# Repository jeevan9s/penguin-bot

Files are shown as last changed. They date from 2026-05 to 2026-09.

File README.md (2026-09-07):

# penguin

> <b>P</b>erception-<b>E</b>nabled <b>N</b>avigation and <b>G</b>eneral-<b>U</b>tility <b>IN</b>telligence

Hybrid differential legged-wheeled biped rover for embodied AI, computer vision, and autonomous navigation.

### Status

> - Controller manufactured and partially assembled.
> - Soldering and hardware validation in progress.
> - Mechanical components currently being printed.

<details>`
<summary><strong>Table of Contents</strong></summary>

- [penguin](#penguin)
    - [Status](#status)
  - [Overview](#overview)
  - [Features](#features)
    - [Controller](#controller)
    - [Mechanical](#mechanical)
  - [Architecture](#architecture)
    - [Systems](#systems)
  - [Electrical](#electrical)
    - [Power System](#power-system)
    - [Microcontroller](#microcontroller)
    - [Motor Drivers](#motor-drivers)
    - [Vision Interface](#vision-interface)
    - [Sensor and I2C Interface](#sensor-and-i2c-interface)
    - [Bugs](#bugs)
  - [Mechanical](#mechanical-1)
    - [Chassis](#chassis)
    - [Leg Assembly](#leg-assembly)
  - [Firmware](#firmware)
    - [Architecture](#architecture-1)
    - [Drivers](#drivers)
    - [Engine](#engine)
      - [State \& System Definitions](#state--system-definitions)
      - [Controllers \& Locomotion](#controllers--locomotion)
      - [Behaviour](#behaviour)
    - [Networking](#networking)
    - [GUI](#gui)
  - [Gallery](#gallery)

</details>

I built penguin cause I wanted to create an intelligent robot from the ground up.

<table>
  <tr>
    <td width="50%">
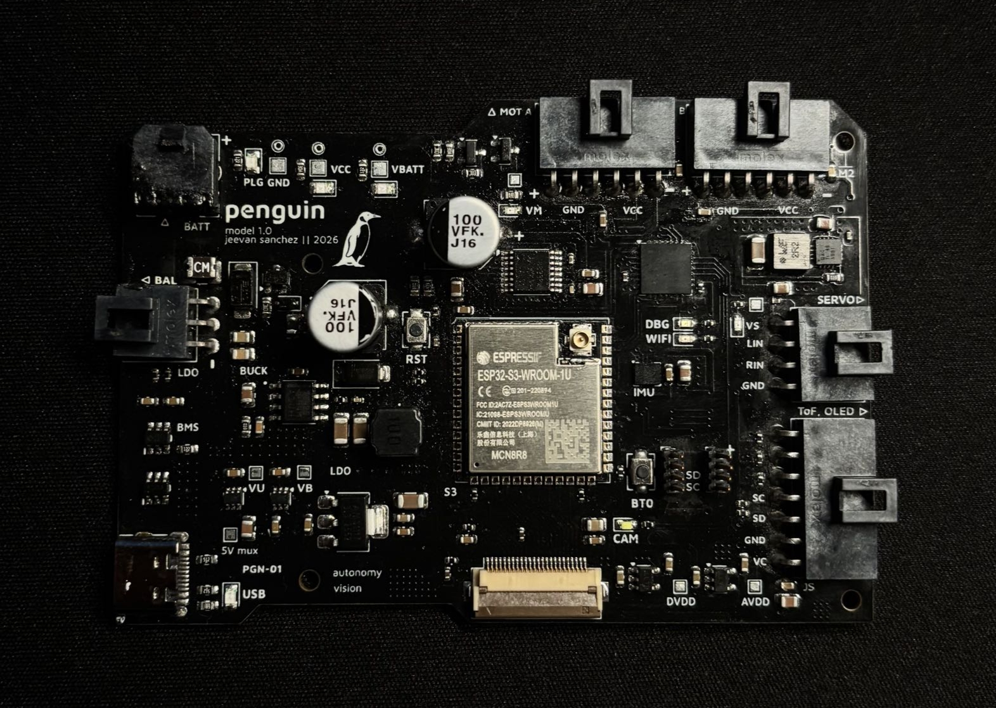
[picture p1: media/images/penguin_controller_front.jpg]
      
    </td>
    <td width="50%">
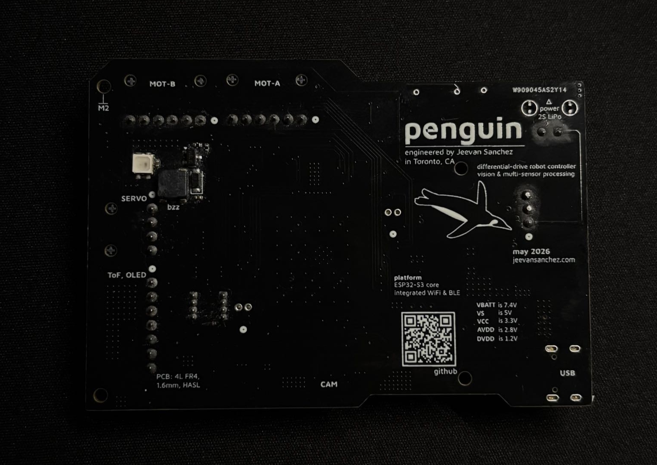
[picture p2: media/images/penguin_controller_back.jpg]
      
    </td>
  </tr>
  <tr>
    <td width="50%">
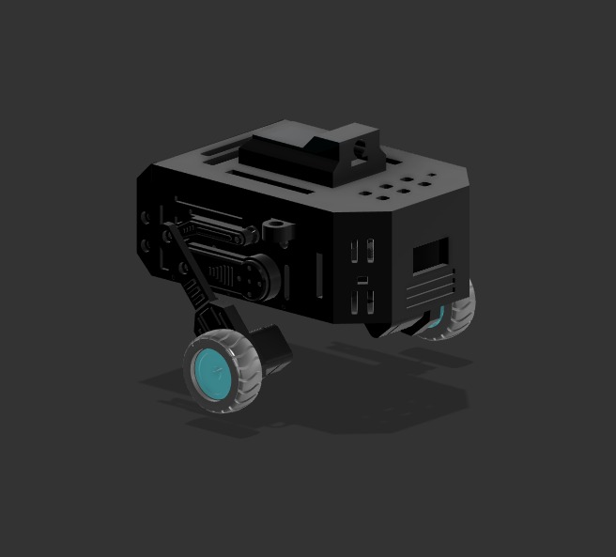
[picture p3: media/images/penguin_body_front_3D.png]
      
    </td>
    <td width="50%">
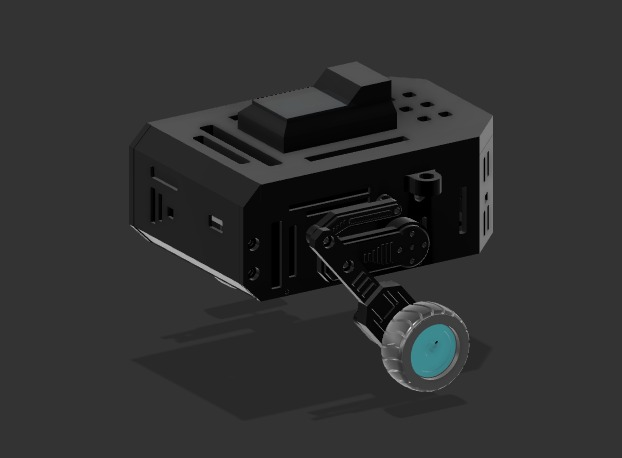
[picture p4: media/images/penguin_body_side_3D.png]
      
    </td>
  </tr>
    <tr>
    <td width="50%">
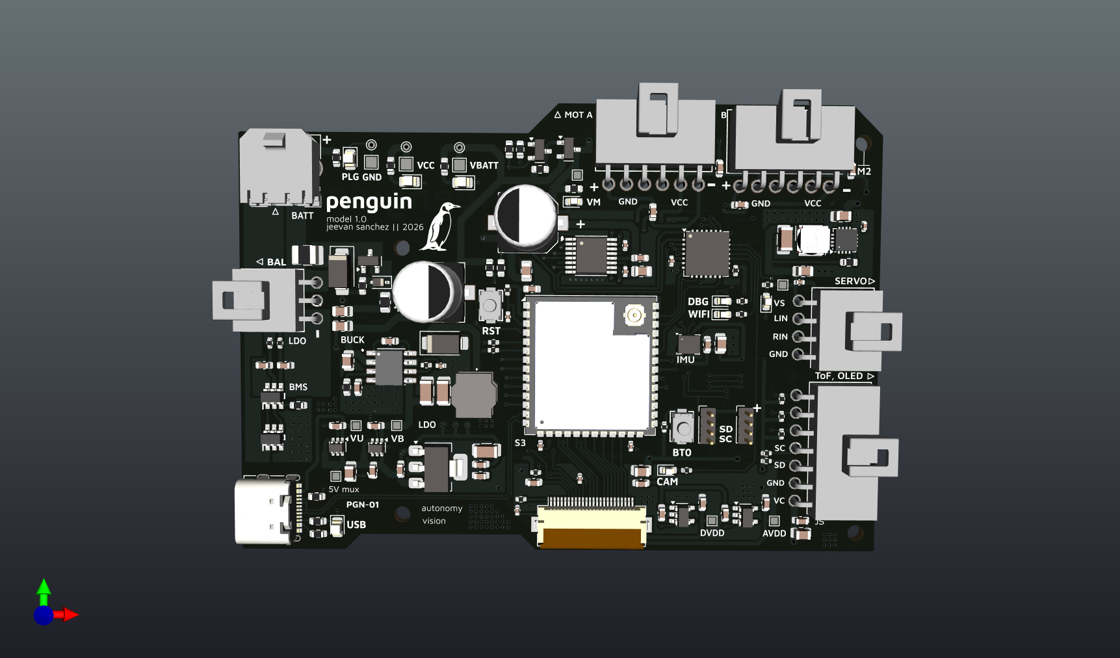
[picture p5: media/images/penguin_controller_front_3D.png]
      
    </td>
    <td width="50%">
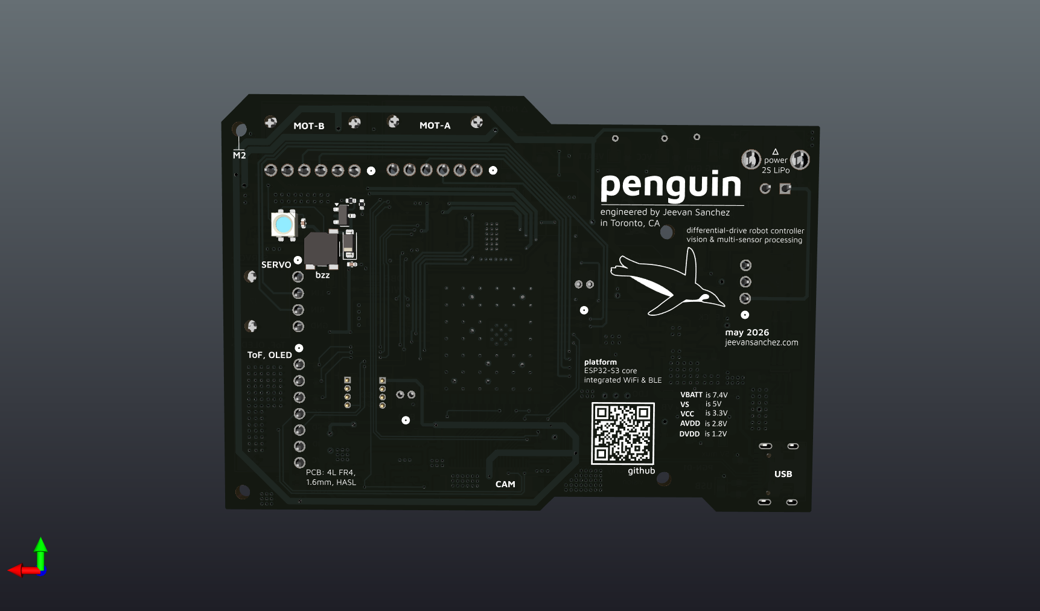
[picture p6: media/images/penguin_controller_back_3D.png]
      
    </td>
  </tr>
</table>

## Overview

Put simply, Penguin is a platform for experimentation with intelligent robotics.

The project began as a simpler, maze-solving rover for a course project (MREN 178 - DSA). My team couldn't deliver the rover in time
so we scaled down. I had already started with hardware, which pushed me to adopt the project into my own, with the intent to expand it past maze-solving.

After that term (Winter '26), I designed a controller PCB and the necessary compoments for the chassis.

Now its September, and I'm tuning PID.

## Features

### Controller

The controller is powered by a 7.4V LiPo Battery and driven by an ESP32-S3 (N16 1U).

Below is a list of features from power circuits to various peripherals.

- Power-entry circuitry with OC/OV protetction, RPP, PI-filter, and dual-mosfet BMS.
- Regulation circuit featuring buck converter, 5V ORing, and LDO for logic power (3V3)
- ESP32-S3 breakout circuitry with USB differential routing, S3 boot mode selection and reset toggle.
- Controlled power delivery via CMOS circuits for main motor power.
- N20 motors with encoders for wheels driven by a DRV8833 chip.
- DS3218 20kg Servo motors for hip joints, driven by PWM signals from S3.
- OV2640 camera with FPC connector and three-level voltage regulation.
- I2C bus with three ToF sensors, OLED screen, and GPIO expander.
- Audible and visual indicators.
- cool silkscreen penguin.

### Mechanical

- Three-layer internal stackup for housing motors, controller board, and routing cables.
- Integrated vents and ports for sensors and devices, air flow, and weight reduction.
- Hybrid locomotion system with wheels and legs.
- Multi-bar leg assembly - pivot arm, mounting arm (hip), leg.

## Architecture

### Systems

## Electrical

This section provides low-level explanations of the significant circuits of each "module" of the controller.

I encourage you to clone the repo or you use [KiCanvas](https://kicanvas.org/) to look at the schematic and board files.

All electronics were designed with **KiCad**.

### Power System

**Power Entry**

<p align="center">
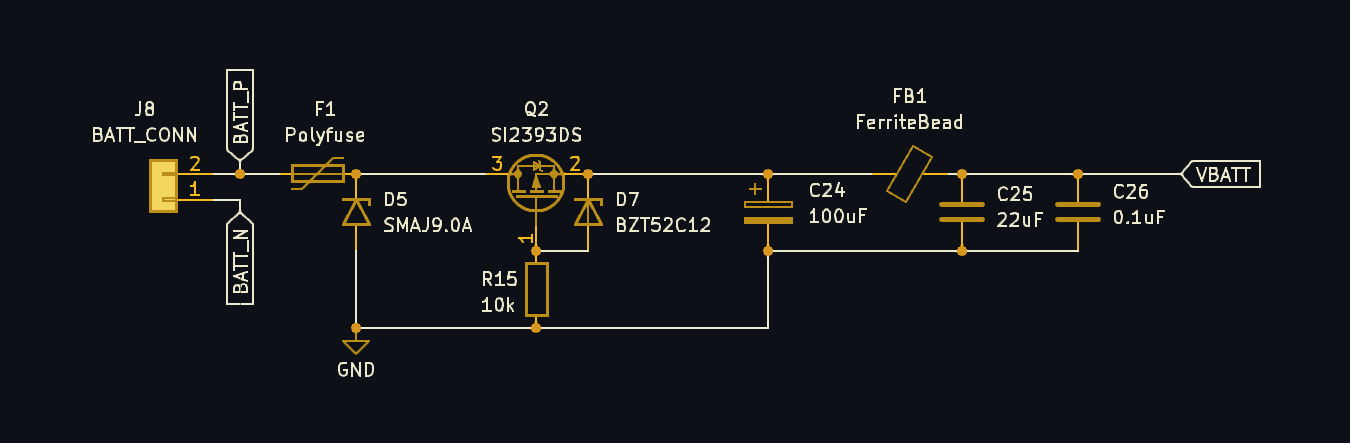
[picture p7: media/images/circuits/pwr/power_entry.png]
  
</p>

The 7.4V battery power enters through a Molex Micro-Fit (3mm Pitch) header, where it is then met with a 12V 7A fuse for over-current protection. A PTC resettable fuse was selected for durability.

The positive battery line is then protected from voltage spikes with a Transient Voltage Supression (TVS) diode placed in paralell for clamping.

- The diode's standoff @ `9V`
- Breakdown @ `10V`
- Clamps @ `15.4V`

The positive line then goes through a Reverse Polarity Protection (RPP) circuit, using a P-Channel MOSFET for lossless efficiency (lower V drop than standard diodes).

A Zener diode and resistor is placed between the MOSFET's gate and source for gate over-voltage protection.

A bulk electrolytic (100μF) capacitor, ferrite bead, and high-frequency (0.1μF) capacitor are then placed to create a third-order low pass filter (π-filter).

- This is used to smooth voltage spikes and reduce EMI.

The ferrite bead was primariy selected for its saturation current and DCR.

The approximate current draw with safety margin $I_{net}$ is 5A.

$I_{\mathrm{sat}} = 1.5 \times I_{\mathrm{net}} \approx 10 A$

Minimize heat dissipation.

$DCR$ is 10Ω

$P_{heat} = DCR \times I_{\mathrm{sat}} \approx 0.25 W$

**Battery-Management-System (BMS)**

<p align="center">
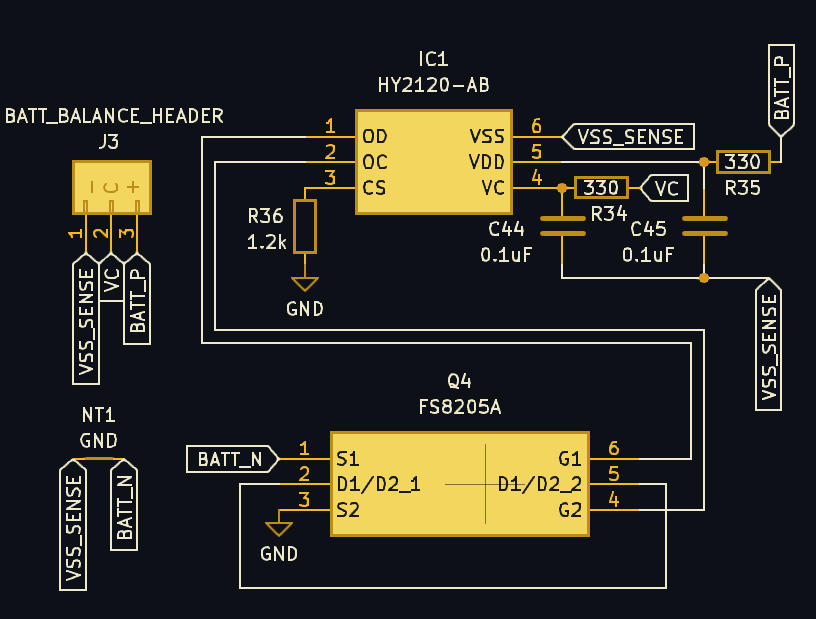
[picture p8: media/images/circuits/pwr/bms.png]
  
</p>

The BMS system uses the negative terminal of the battery and features a `HY2120` protection IC with a dual-mosfet to form the system's **GND**.

The IC uses the balance tap of the battery (VC ~ 3.7V nominal) to monitor the level of Cell 1, while using the main positive terminal (VDD ~ 7.4V nominal) to monitor Cell 2.

This allows the IC to indepdently track each cell's voltage and trigger the dual-MOSFET to cut off power if either cell suffers from overcharge or overdischarge.

**Voltage Regulation (I)**

<p align="center">
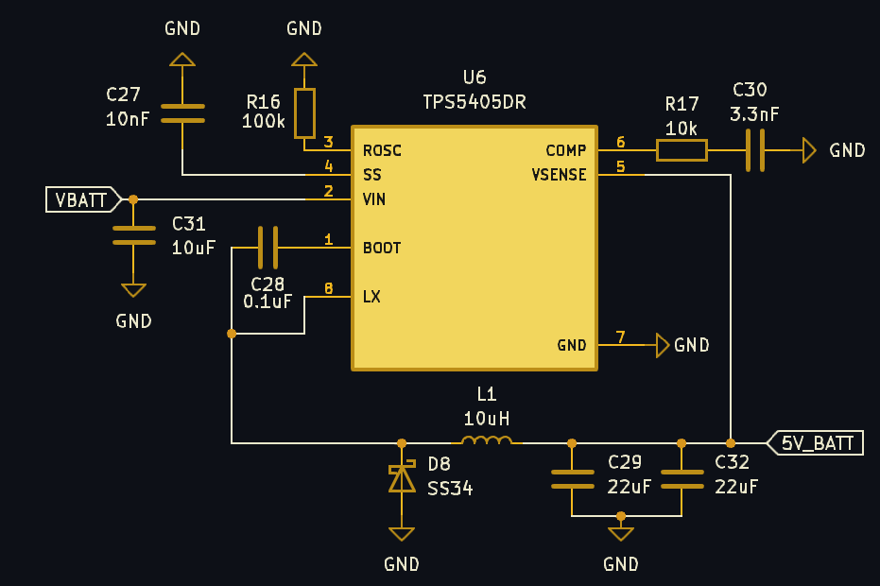
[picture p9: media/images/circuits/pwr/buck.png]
  
</p>

The controller uses a cascade regulation system, starting with the `TPS5405DR` buck converter.

The input voltage is `VBATT` (7.4V), after the protection and filtering circuitry, and the output is 5V.

The $R_{osc}$ value will determine the switching frequency of the converter.

Switching frequency is governed by the relationship.
$$R_{\text{OSC}} (\text{k}\Omega) = 21.82 \cdot f_{\text{SW}}^{-1.167}$$

I chose a value of `100kΩ` for a $f_{SW}$ of approximately `271 kHz`

For the soft-start capacitor $C_{ss}$ , I chose a value of `10nF` for a soft-start time of `5ms`

The values below were taken from the [TPS5405DR Datasheet](https://www.ti.com/lit/gpn/tps5405)

$$
C_{SS} = \frac{t_{SS} \cdot I_{SS}}{V_{REF}}
$$

$$
C_{SS} = \frac{(5\,\mathrm{ms})(2\,\mathrm{\mu A})}{0.8\,\mathrm{V}}
= 12.5\,\mathrm{nF}
\approx 10\,\mathrm{nF}
$$

The inductor values were chosen using the equation below.

$$
L=\frac{V_{out}\left(V_{in}-V_{out}\right)}
{V_{in}f_{sw}\Delta I_L}
$$

Using our calculated $f_{sw}$ from above and our voltage requirements (8.4V in, 5V out):

$$
L=
\frac{(5\,\mathrm{V})(8.4\,\mathrm{V}-5\,\mathrm{V})}
{(8.4\,\mathrm{V})(525\,\mathrm{kHz})(0.3\,\mathrm{A})}

\approx
10\,\mathrm{\mu H}
$$

The Schottky diode is rated for the `2A` output current and `8.4V`

**5V ORing**

<p align="center">
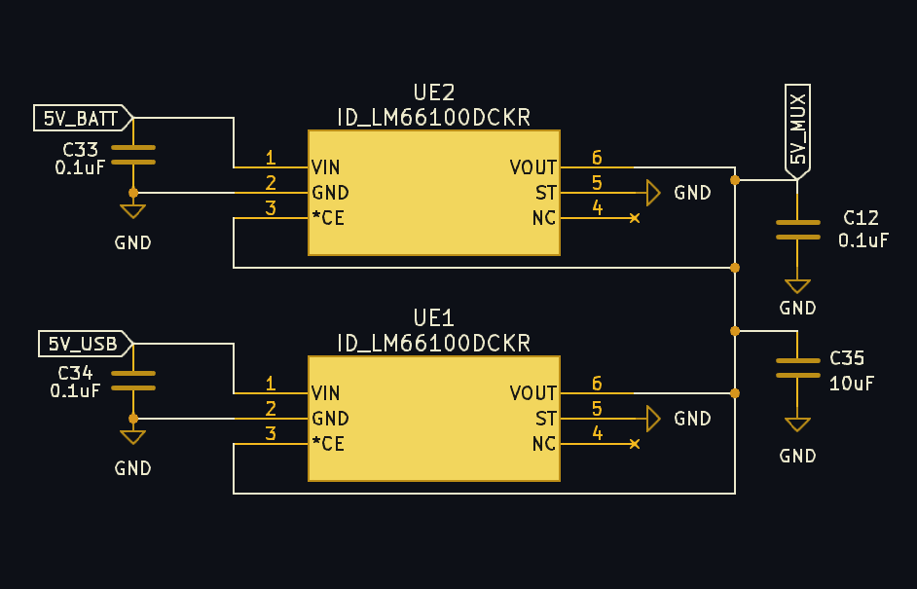
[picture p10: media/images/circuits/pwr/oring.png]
  
</p>

The `5V` rails from both USB and the buck converter are combined using an OR-ing circuit (Dual Ideal Diodes) to prevent backfeeding before feeding the second stage of regulation.

In this configuration, the outputs of both `LM66100` ideal diode controllers are tied together to form the shared `5V` rail. The `CE` pins of each device are also tied to the output rail, ensuring both controllers are only enabled once the rail is present

**Voltage Regulation (II)**

<p align="center">
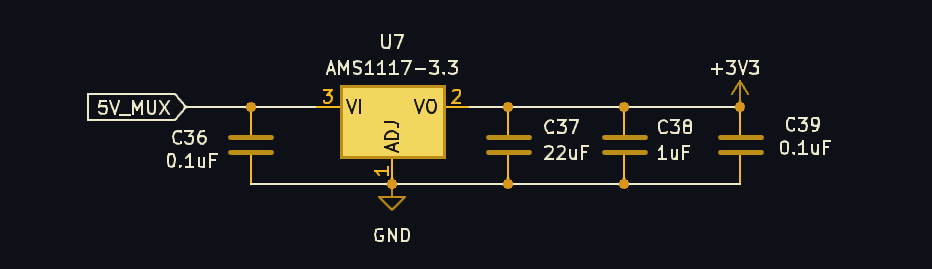
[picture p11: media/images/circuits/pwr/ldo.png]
  
</p>

The second stage of voltage regulation involes a Low-Dropout Regulator (LDO), the `AMS1117`

It is fed the combined `5V` rail from the OR-ing circuit to produce the controller's logic-level voltage: `3V3`

**Controlled Motor Power Delivery**

<p align="center">
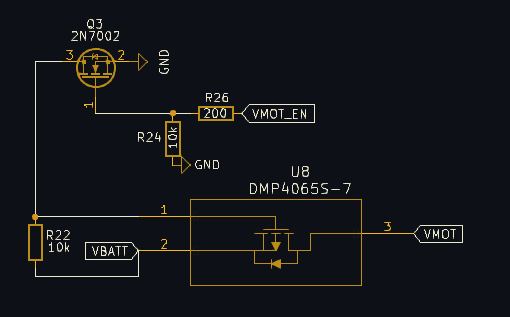
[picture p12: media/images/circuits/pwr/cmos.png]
  
</p>

The power for the N20 and Servo motors is controlled using a complementary-MOSFET (CMOS) setup, driven by a digital `HIGH` from the S3.

- When the control signal is low or floating, the N-channel MOSFET remains off and a pull-up resistor holds the gate of the P-channel MOSFET at the supply voltage, keeping it disabled and disconnecting the load rail.

- When the control signal is driven high, the N-channel MOSFET turns on and pulls the P-channel gate low, creating sufficient gate-source voltage to enable conduction and connect the supply to the load.

This controlled power line, `VMOT = 7.4V` powers the supply voltage of the `DRV8833` chip, and is converted via local buck converter to produce `VSERVO = 5V`

**Voltage Sensing**

A resistor divider circuit is used to produce a signal to be read by the S3's internal ADC.

- $R_1 = 100\,\mathrm{k\Omega}$
- $V_{batt} = 7.4\,\mathrm{V}$
- $V_{out} = 2.8\,\mathrm{V}$

$$
R_2 = \frac{R_1 \cdot V_{out}}{V_{batt} - V_{out}}
$$

$$
R_2 = \frac{100\,000 \cdot 2.8}{7.4 - 2.8}
= 50\,\mathrm{k\Omega}
\approx 47\,\mathrm{k\Omega}
$$

### Microcontroller

The controller is driven by an ESP32-S3-WROOM-1U-N16 microcontroller.

The `U` and `N16` model was selected for layout flexibility and memory capacity (16MB).

A `MCP23017` GPIO expander was used to accomodate space for all digital inputs/outputs (via `I2C`)

**Digital IO**

<p align="center">
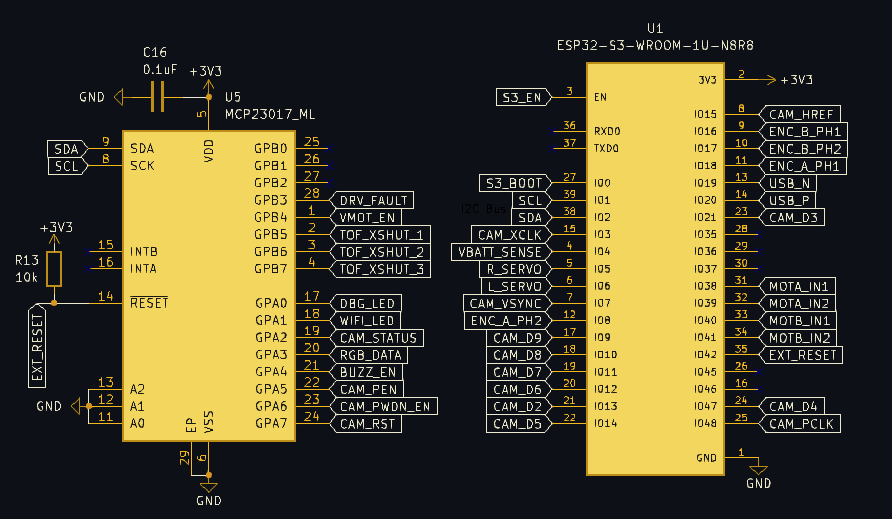
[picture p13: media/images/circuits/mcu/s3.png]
  
</p>

**Mode Select and Reset Toggle**

<p align="center">
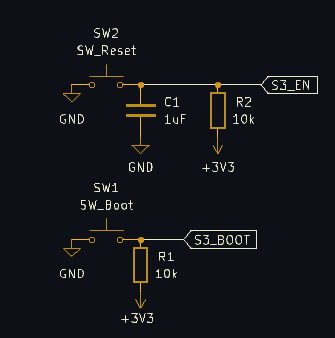
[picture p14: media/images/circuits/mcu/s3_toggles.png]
  
</p>

The S3 can be put into **BOOT** mode and **RESET** with onboard buttons.

**BOOT** mode determines whether the chip runs existing code from flash memory or waits to download new firmware.

- The ESP32 samples the **BOOT** pin (`GPIO0`) during reset to determine the boot mode.
- It is **active-low**: when pulled to **GND** during reset, the chip enters UART bootloader mode for flashing firmware.
- The circuit uses a momentary push-button to **GND** and a `10kΩ` pull-up resistor to ensure a defined high state during normal operation.

| BOOT0 Level | Boot Mode |
| --- | --- |
| HIGH | Programming Mode |
| LOW | Memory Mode |

**RESET** controls the Enable (EN) pin which is the ON/OFF (reset) switch for the ESP32.

- It is **active-low**: when pulled to **GND** it turns off the chip, and when released, it restarts.
- The circuit consists of a momentary push-button, a pull-up resistor to ensure the chip is enabled by default, and a `1µF` capacitor to filter out button noise.

### Motor Drivers

The `N20` wheel hub motors are driven by a `DRV8833` chip, and their encoder signals are routed to digital pins on the `S3`.

They are connected via 6-Pin Molex Nano-Fit (2.50mm Pitch) headers, and feature decoupling across the motor terminals and on the encoder power supply.

<p align="center">
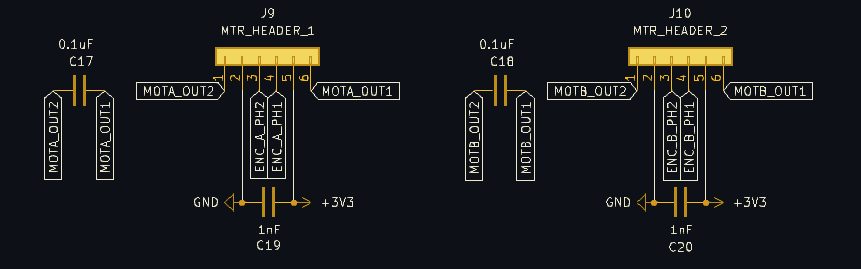
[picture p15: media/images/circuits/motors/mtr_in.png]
  
</p>

The **Servo** hip motors are driven by PWM signals from the `S3`, and are connected by a single 4-Pin Molex Nano-Fit header.

The connector has decoupling on the power supply, and series resistors on the signal lines to improve signal integrity and reduce noise.

<p align="center">
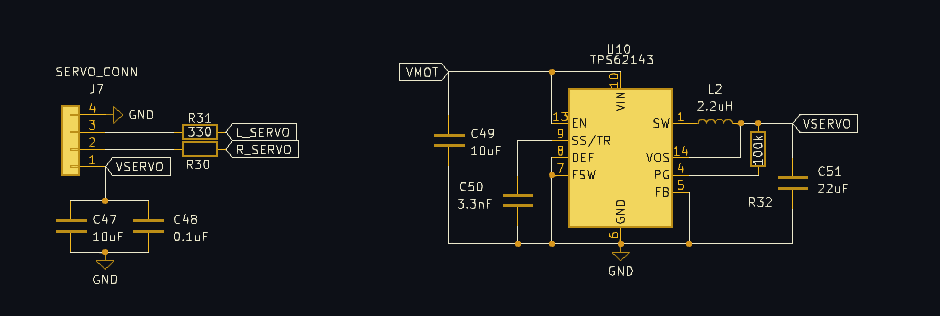
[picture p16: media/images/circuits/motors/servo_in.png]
  
</p>

### Vision Interface

The controller interfaces with an `OV2640` camera via FPC-connector.

The camera is configured in **8-bit** mode using adjacent digital pins for frames.

<p align="center">
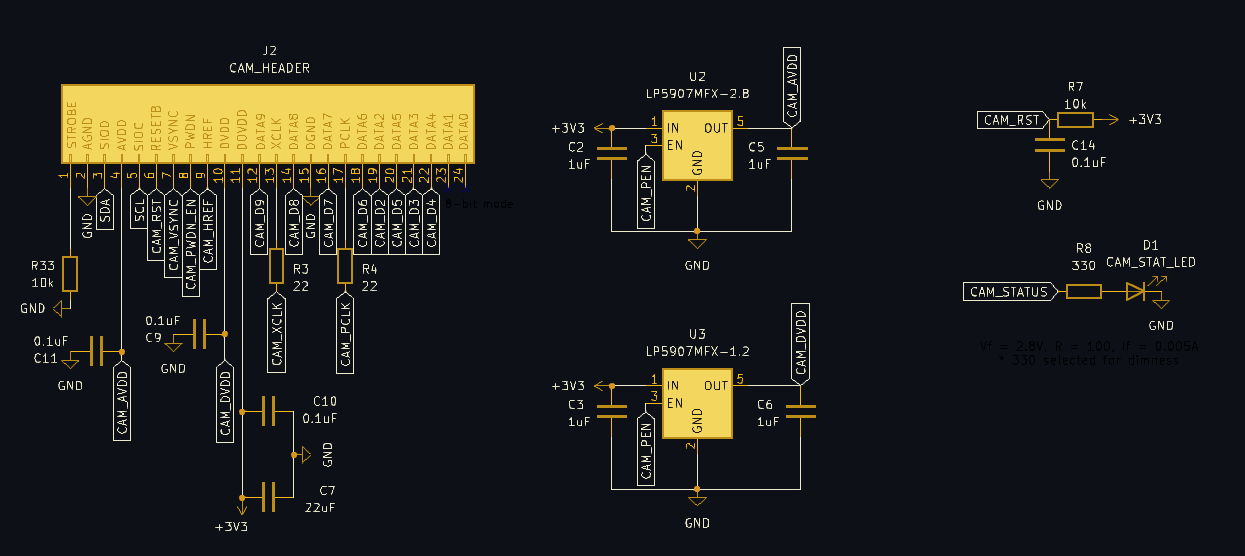
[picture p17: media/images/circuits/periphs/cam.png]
  
</p>

Power supply is divided into three levels:

- `DVDD`: **1.2V**
- `AVDD`: **2.8V**
- `DOVDD`: **3.3V**

These conversions are acheived through the use of fixed-output-voltage LDOs (`LP5907MFX`) with local decoupling.

Series low-resistance resistors were added on the camera's clock signals (PCLK, XCLK) in series for signal integrity and EMI reduction.

- I used only `S3` pins, not expander pins, for the data pins `D2-D9` and `HREF`, `VSYNC` pins.

### Sensor and I2C Interface

The controller interfaces with three `VL53L0X` Time-of-Flight (ToF) sensors for ranging (obstacle detection, SLAM - potentially).

This interface is achieved through `I2C`.

The sensors are connected through a single 7-Pin Molex Nano-Fit header, connecting the sensor power, I2C clock and data signals, and the shutdown `XSHUT` pins of each sensor.

Decoupling capacitors and shutdown pull-ups are placed locally.

<p align="center">
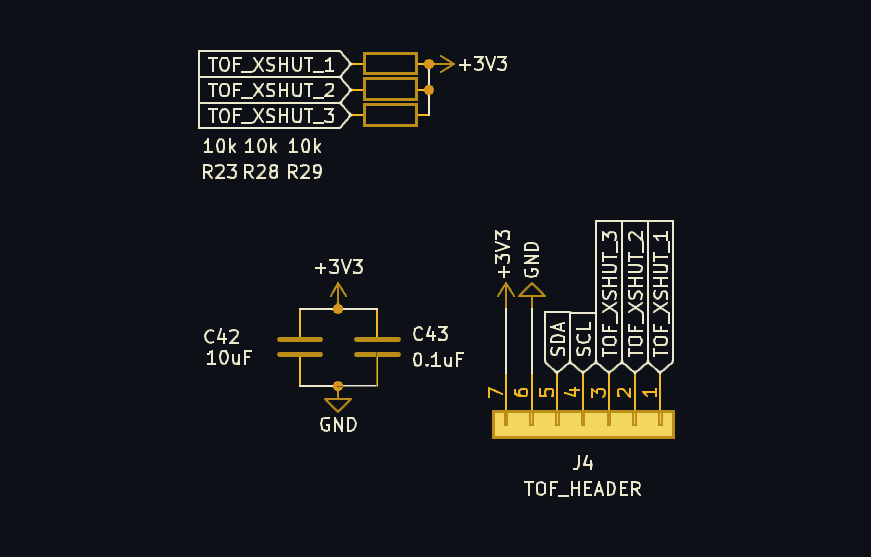
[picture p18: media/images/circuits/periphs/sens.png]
  
</p>

**Additional I2C Devices**

- IMU (LSM6DSL)
- Mini OLED Screen
- OV2640 Cam

**Indicator Components**

- RGB LED
- Passive LEDs for simple indication
- Buzzer for audible indication

### Bugs

- Misoriented cam header -- fixed with an extenison board + B-Type FPC cable
- DRV8833 VM and VINT pins missing GND connection
- Buzzer and RGB LED pins need clock signal but wired to MCP pins.

## Mechanical

This section provides insight on the mechanical components of Penguin: the chassis and leg assembly.

In no way am I a CAD-expert, so this was definitely a learning experience with lots of iteration.

Projected geomtery was clutch.

I used Fusion360 to design everything.

### Chassis

The chassis consists of several components attatched with pegs and magnets.

<p align="center">
  
</p>

**Base Plate**

The base plate forms the start of the internal stack-up.

It contains Servo pads for the hip motors to rest on, a port for an ON/OFF switch, and a battery slot with vents.

It acts as the "floor" of the Servo bay and the bottom of the chassis.

It connects to the rest of the chassis through pegs to insert into the inside face of each wall, as well as the nose.

<p align="center">
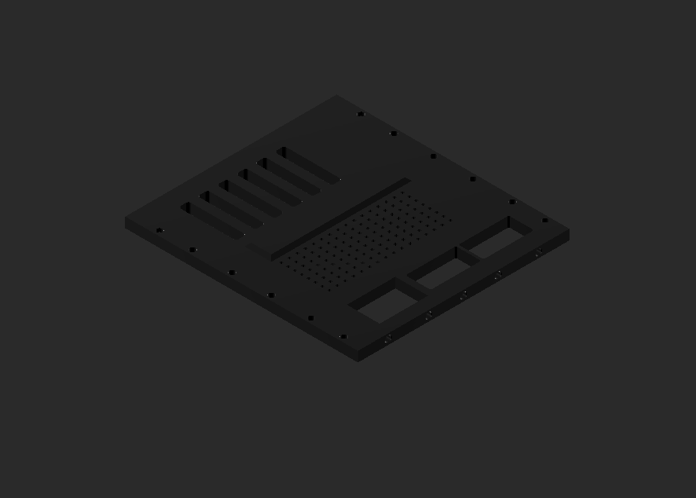
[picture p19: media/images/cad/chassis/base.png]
  
</p>

**Side Walls**

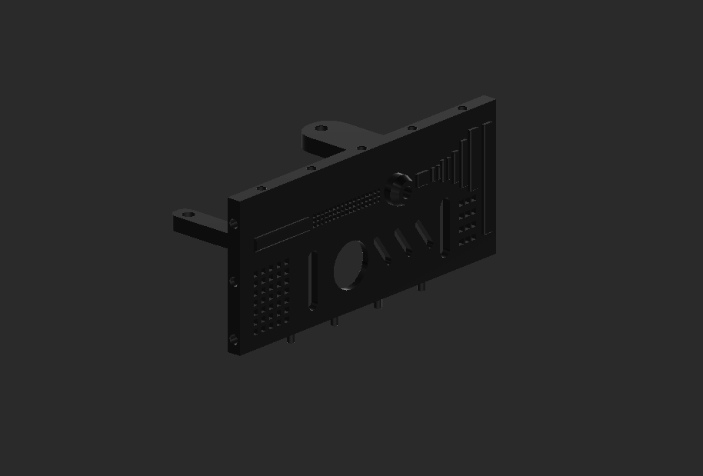
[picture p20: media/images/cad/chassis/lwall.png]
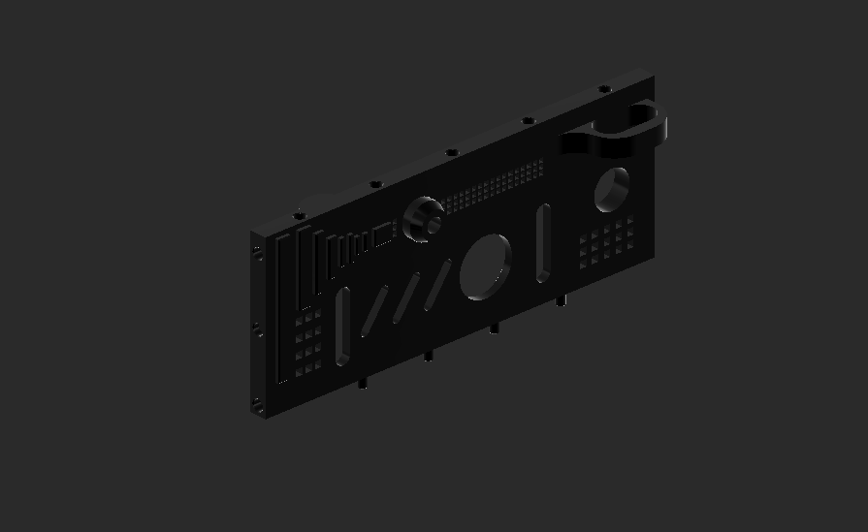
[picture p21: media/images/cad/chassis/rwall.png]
<table><tr><td width="50%"></td><td width="50%"></td></tr></table>

The side-walls enclose the internal stack-up, and provide mounting points for several chassis components.

Mounting tabs are on the inside of each wall for board mounting.

They have cutouts for the Servo shafts, arm joints, and house components like the external antenna.
The top face has short holes for magnets that align with holes on the lid.

**Nose**

<p align="center">
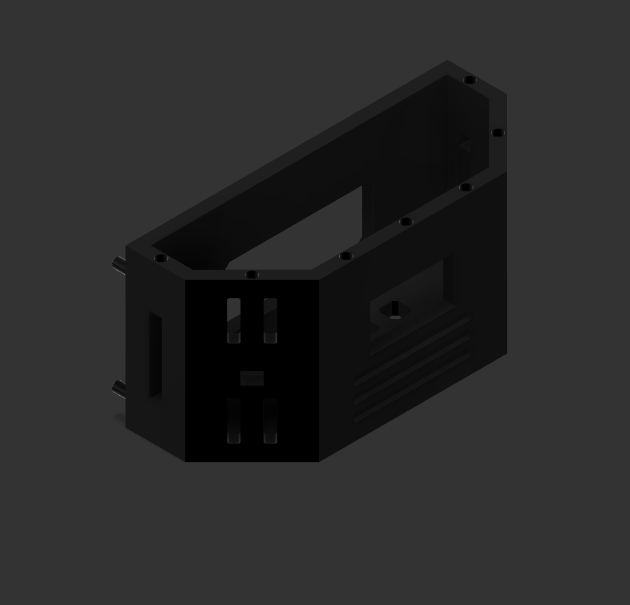
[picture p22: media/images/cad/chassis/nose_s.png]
  
</p>

The nose contains ports for the ToF sensors, and an OLED screen.

There is also an open face cable port connecting to the controller bay for routing.

It mounts to each walls with pegs and magnets, as well as to the base plate.

**Stern**

<p align="center">
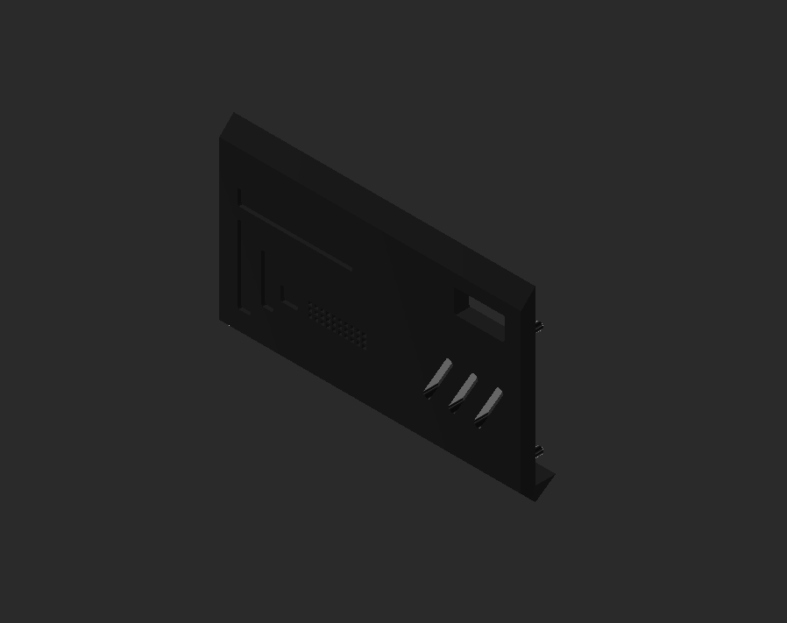
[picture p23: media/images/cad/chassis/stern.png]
  
</p>

The stern features a USB-port and snaps to the walls via pegs.

**Lid**

<p align="center">
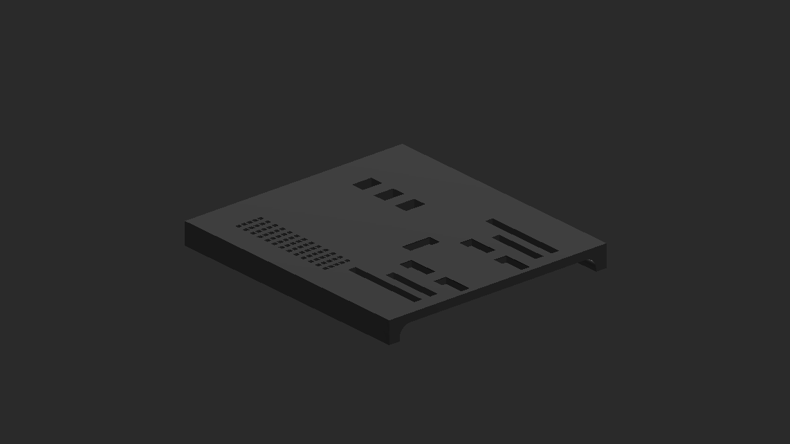
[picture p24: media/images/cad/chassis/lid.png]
  
</p>

The lid contains a magnet cutouts for mounting the camera mount, and is magnetically mounted on the top surface of the walls and nose.

**Camera Mount**

<p align="center">
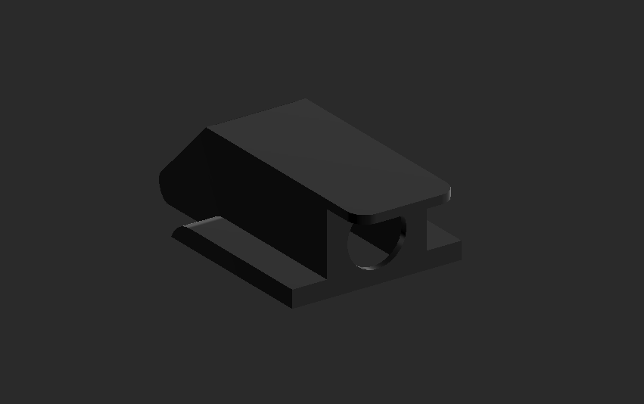
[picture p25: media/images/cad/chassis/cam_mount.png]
  
</p>

The mount features a porthole for the OV2640 camera lens, and corresponding magnet cutouts for mating with the roof.

### Leg Assembly

<p align="center">
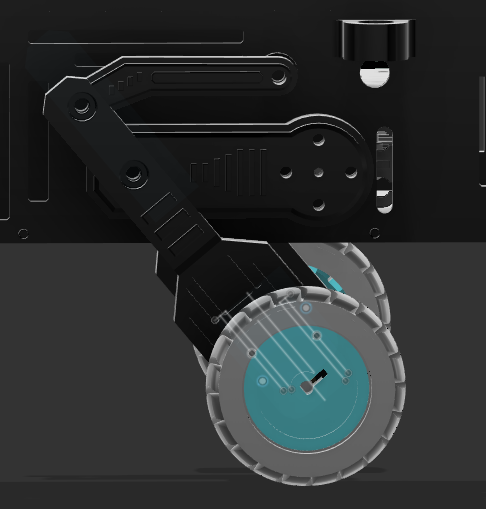
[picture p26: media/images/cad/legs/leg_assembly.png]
  
</p>

The leg assembly consists of the Servo mounting arm, pivot arm, and the wheel hub assembly.

**Mounting Arm**

<p align="center">
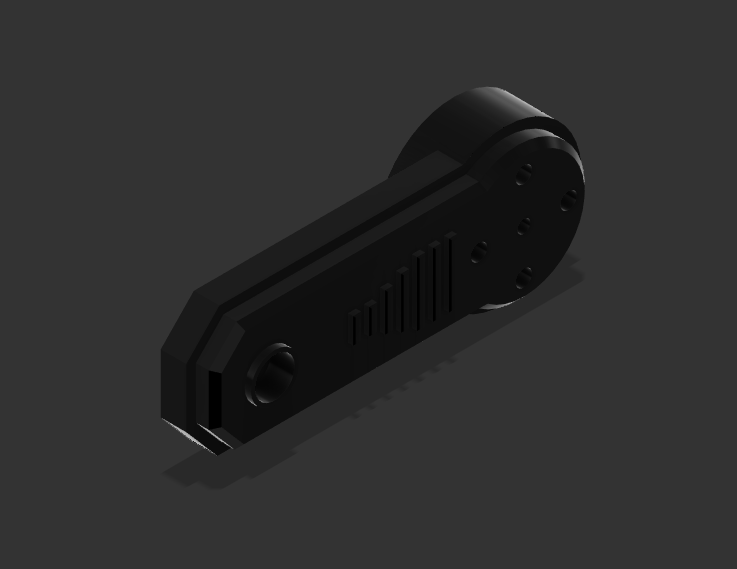
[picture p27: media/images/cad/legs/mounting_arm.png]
  
</p>

This is the contact point between the leg assembly and the hip motor, it's responsible for driving the assembly.

The Servo uses the disc-horn, and fits into a cutout on the mounting arm, and is secured in with the stock machine screw into the shaft.

The end of the arm mounts onto the wheel hub assembly using bearings on each hole, an M3 shoulder bolt, and a nut.

**Pivot Arm**

<p align="center">
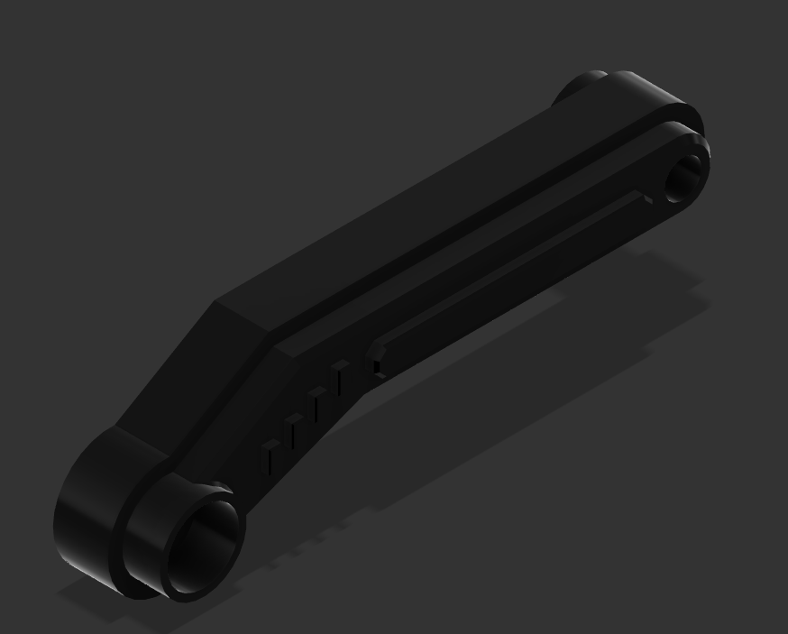
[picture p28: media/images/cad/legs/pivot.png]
  
</p>

The pivot arm maintains proper orientation for the assembly as the suspension moves up and down.

It uses the same mounting as the mounting arm (bearing, shoulder bolt, nut), and is mounted slightly higher at a 40° angle on the wheel hub assembly.

**Wheel Hub Assembly**

<p align="center">
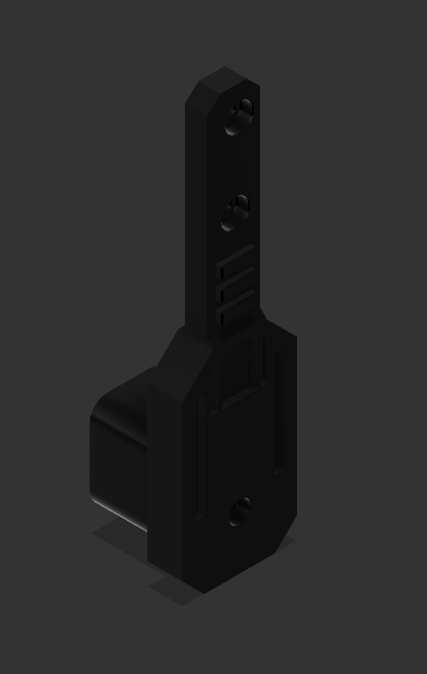
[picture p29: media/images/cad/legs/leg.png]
  
</p>

This component houses the N20 motors through a cutout and U-Channel cover to secure them.

The top of the assembly contains the two mounting points for the pivot and mounting arms.

Cables are routed up the back side of it.

## Firmware

Firmware was written in `C++` using the `Arduino` framework via `PlatformIO`.

All implementations can be found in the [`firmware/src`](firmware/src) directory.

### Architecture

<p align="center">
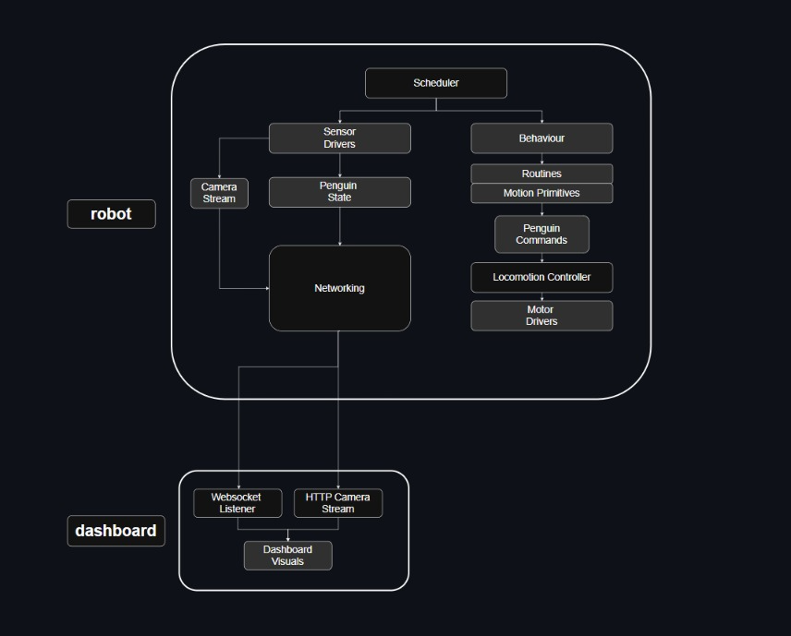
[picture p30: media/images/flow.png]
  
</p>

The firmware design is divided into three distinct layers:

- **HAL Drivers**
  - Abstraction of interfaces with hardware components.
- **Core Engine**
  - Controllers and state definitions
- **Networking**
  - Telemetry for GUI

### Drivers

Hardware drivers are used to abstract hardware interfaces for motors and sensors.

Each driver exports a class that follows a consistent structure:

```cpp
class Driver {
  public:
    Driver(uint8_t pin);
    bool begin();
    Data read(); // return type unique to hardware
    void run();
};
```

Sensory drivers such as ToFs, IMU, and camera export reads.

Actuator drivers export runs, but the DC motor driver exports a read for the encoders.

In terms of integration, drivers are instantiated at the application level (main.cpp), and are invoked by the scheduler for telemetry, and by the locomotion engine for motor control.

### Engine

The engine layer encapsulates all state machine, control, and behavioural logic into several classes.

- State & System Definitions
  - Data types, schema for global data instance
- Controllers and Locomotion
  - PID utility class, motor control
- Behaviour
  - Motion primitives and routines

#### State & System Definitions

This section defines shapes for all system objects, including IMU, ToF, and motor data.

<details>
<summary>IMU Data Object</summary>

```cpp

struct IMUData
{
  float accX; // g
  float accY;
  float accZ;

  float gyX; // dps
  float gyY;
  float gyZ;

  float temp; // C

  Rotation angles;
};

```

</details>

This and other data types are placed in a `PenguinState` struct which acts as the global state for telemetry lookup and velocity controllers. 

Additionally, it implements a `PenguinCommands` field, which is observed by locomotion controllers and updated by mmotion primitives. 
- Commands specify desired pitch, RPM, and hip angles. 

#### Controllers & Locomotion
The locomotion layer manages the low-level **movement** of the robot. 

It is blind to routines; it doesn't know *when* to move but it knows how to adjust its motion given a command (orchestrated autonomously by the Behaviour layer). 

A utility PID class is used as the basis for locomotion controller. 

It calculates an error value as the difference between a target setpoint and a mesaured proces variable, then applies a correction based on proportional, integral, and derivative terms, to smoothly drive the controller toward its desired state. 

$$u(t) = K_p e(t) + K_i \int_{0}^{t} e(\tau) d\tau + K_d \frac{de(t)}{dt}$$

The layer defines two important controllers: 
- **Balance Controller**
  - Produces an optimal RPM based on a target pitch. 
  - Uses the IMU pitch rate as derivative term in the PID Equation. 

- **Velocity Controller**
  - Produces an optimal PWM based on a target RPM. 
  - Target RPM is split into differential-drive inputs to be fed into two distinct controllers (L, R). 
    - $$v_{\text{lr}} = v_{\text{fwd}} - v_{\text{turn}} + v_{\text{corr}}$$

The main Locomotion engine then wraps these controllers within an update method to observe the `RobotCommands` struct and adjusts accordingly. 
- Hip motors are also driven here for stance adjustment. 

#### Behaviour
The behaviour layer defines the buidling blocks of Penguin's movement: 
- Motion Primitives
  - Movement actions. 
- Routines
  - Sequences of motion primitives. 

Primitives directly update `RobotCommands`, and form key positions and stances. 

Routines are simply **sequences** of motion primitives, and are tracked using a step-counter and a non-blocking timer. 
- Transitions are smoothed using **Linear Interpolation**

The routine class exports an `update` method for switching between different routines. 

This method is used in the `Behaviour` implementation. 
- Currently it autonomously runs a default cycling routine with obstacle avoidance using the ToF sensors and reverse primitives. 

### Networking
This layer leverages an asynchronous HTTP server and Websockets for streaming data to the GUI. 

The `ESPAsyncWebServer.h` is wrapped in a class `HTTPServer` which implements `begin` and `update` methods which initializes the Websocket connection, and sends the telemetry packet. 

The firmware data packet is serialized into a JsonDocument before streaming. 

The telemetry packet contains:
- Motor Data 
  - RPM, position, running boolean
- IMU Data 
  - Pitch, roll, yaw, three-axis acceleration
- ToF Data (For each sensor)
  - Proximity in mm
  - Obstacle Detection boolean
- Battery Data
  - SOC
  - Connected boolean

The payload updates are orchestrated by the **Scheduler**

| Component | Update Frequency | Update Period (Interval) |
| :--- | :--- | :--- |
| **IMU** | 100 Hz | 10 ms |
| **Motors** | 50 Hz | 20 ms |
| **TOF Sensors** | 25 Hz | 40 ms |
| **Battery Data** | 2 Hz | 500 ms |

The live camera feed is streamed **directly** over HTTP. 

**Camera Stream**

The camera driver captures frames as JPEG images and exposes them through the controller's HTTP server at:

```text
http://<controller-ip>/stream
```

The endpoint uses a `multipart/x-mixed-replace` response with a `frame` boundary, allowing a browser to display the feed directly as an MJPEG stream. The dashboard uses this endpoint as the source of an `<img>` element, so no additional decoding or polling loop is required on the client.

The current capture configuration is:

- `VGA` frame size (`640 x 480`)
- JPEG pixel format
- JPEG quality setting of `10`
- Two frame buffers using `CAMERA_GRAB_LATEST`
- Approximately `30 ms` delay between released frames to limit stream pressure

Each request owns its stream state and releases the camera frame buffer when the frame has been sent or the client disconnects. The camera must be initialized before the HTTP server is used; the root endpoint at `http://<controller-ip>/` returns `penguin --online` as a simple connectivity check.

### GUI
The dashboard (GUI) is developed in Next.js and is ran as a local web-app. 

It displays:
- A frame view of the live camera feed.
- Three.js & IMU driven board visualization
- Proximity data visuals 
- Spedometer view for motor data

The app simply listens to the streamed Websocket, extracts the payload, and populates the according data objects.

## Gallery

<p align="center">
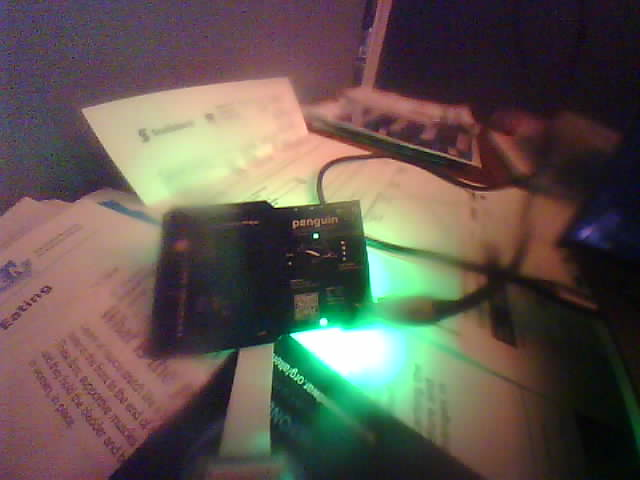
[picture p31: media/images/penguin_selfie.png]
  
</p>

<p align="center">
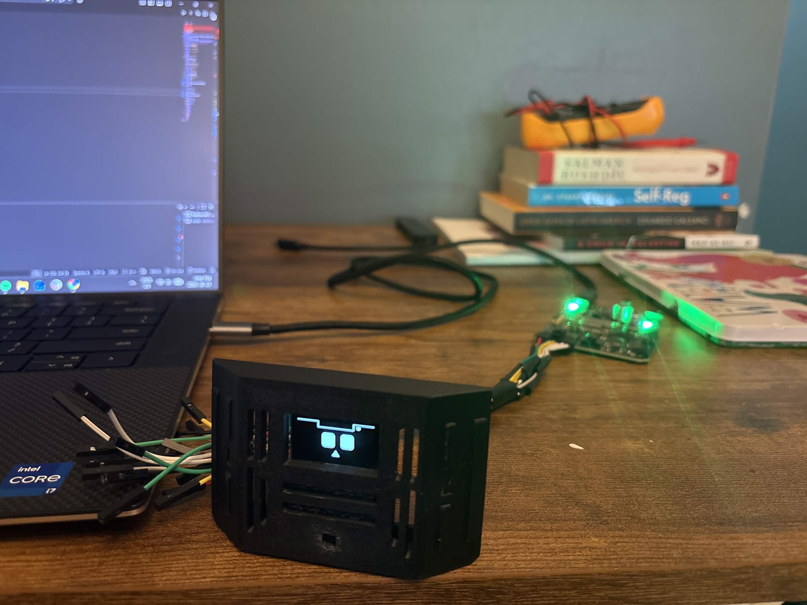
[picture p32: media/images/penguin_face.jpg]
  
</p>

<p align="center">
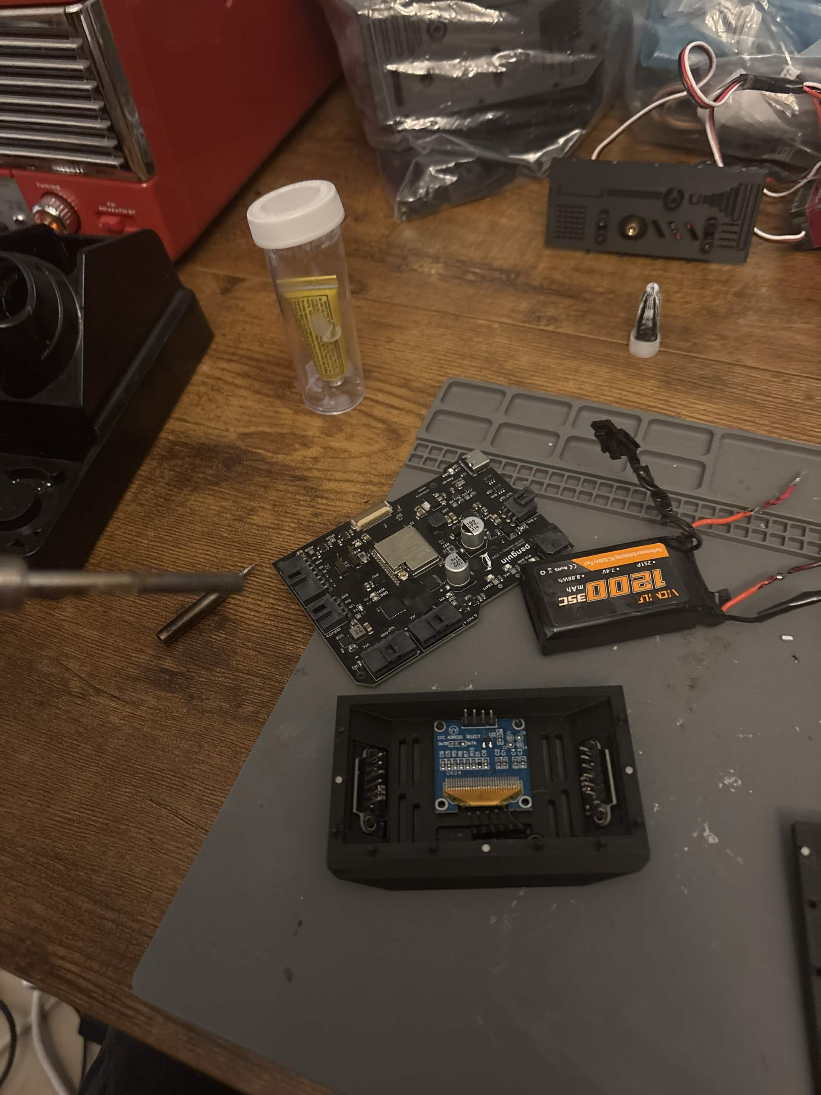
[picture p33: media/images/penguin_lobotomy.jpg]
  
</p>

<p align="center">
  
</p>

---
Jeevan Sanchez, 2026

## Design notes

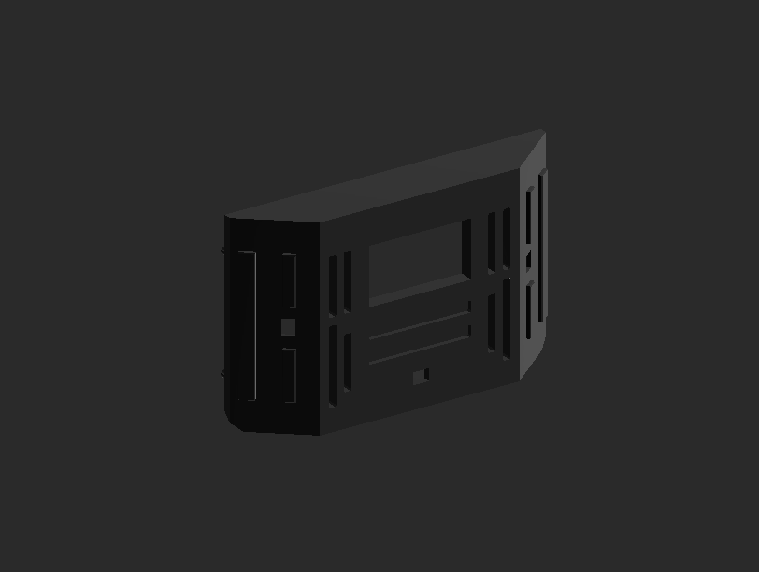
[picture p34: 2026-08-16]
media/images/cad/chassis/nose.png

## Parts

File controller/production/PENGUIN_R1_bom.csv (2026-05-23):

Reference | Value | Datasheet | Footprint | Qty | DNP | Digikey | LCSC
BZ1 | SMT-0540-S-R |  | SMT-0540-S-R:XDCR_SMT-0540-S-R | 1 | DNP
C24 | 100uF | ~ | EEE_FK1V101P:CAP_EEEFK1V101P | 1 | DNP | ZK1V101XV
C40 | 100uF | ~ | EEE_FK1V101P:CAP_EEEFK1V101P | 1 | DNP | ZK1V101XV
D5 | SMAJ9.0A | https://www.littelfuse.com/media?itemid=75e32973-b177-4ee3-a0ff-cedaf1abdb93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 | Diode_SMD:D_SMA | 1 | DNP | SMAJ9.0ABTR-ND
F1 | Polyfuse |  | Fuse:Fuse_1210_3225Metric_Pad1.42x2.65mm_HandSolder | 1 | DNP | F8137TR-ND
J3 | BATT_BALANCE_HEADER | ~ | MOLEX_NANO_3:CONN_SD-105313-100_03_MOL | 1 | DNP | WM14973-ND
J4 | TOF_HEADER | ~ | MOLEX_NANO_7:CONN_SD-105313-100_07_MOL | 1 | DNP | WM16898-ND
J7 | SERVO_CONN | ~ | MOLEX_NANO_4:CONN_SD-105313-100_04_MOL | 1 | DNP | WM14974-ND
J8 | BATT_CONN | ~ | MOLEX_MICRO_2:MOLEX_436500204 | 1 | DNP | WM1875-ND
J9 | MTR_HEADER_1 | ~ | MOLEX_NANO_6:CONN_SD-105313-100_06_MOL | 1 | DNP | WM16893-ND
J10 | MTR_HEADER_2 | ~ | MOLEX_NANO_6:CONN_SD-105313-100_06_MOL | 1 | DNP | WM16893-ND
TP1 | GND_TP_PAD | ~ | TestPoint:TestPoint_Pad_1.5x1.5mm | 1
TP2 | GND_TP_DRILL | ~ | TestPoint:TestPoint_THTPad_D1.0mm_Drill0.5mm | 1
TP3 | VBATT_TP_PAD | ~ | TestPoint:TestPoint_Pad_1.5x1.5mm | 1
TP4 | VBATT_TP_DRILL | ~ | TestPoint:TestPoint_THTPad_D1.0mm_Drill0.5mm | 1
TP5 | 3V3_TP_PAD | ~ | TestPoint:TestPoint_Pad_1.5x1.5mm | 1
TP6 | 3V3_TP_DRILL | ~ | TestPoint:TestPoint_THTPad_D1.0mm_Drill0.5mm | 1
TP7 | VMOT_TP_PAD | ~ | TestPoint:TestPoint_Pad_1.0x1.0mm | 1
TP8 | 5V_USB_TP_PAD | ~ | TestPoint:TestPoint_Pad_1.0x1.0mm | 1
TP9 | 5V_BATT_TP_PAD | ~ | TestPoint:TestPoint_Pad_1.0x1.0mm | 1
TP10 | 5V_MUX_TP_PAD | ~ | TestPoint:TestPoint_Pad_1.0x1.0mm | 1
TP11 | CAM_DVDD_TP_PAD | ~ | TestPoint:TestPoint_Pad_1.0x1.0mm | 1
TP12 | CAM_AVDD_TP_PAD | ~ | TestPoint:TestPoint_Pad_1.0x1.0mm | 1
TP13 | VSERVO_TP_PAD | ~ | TestPoint:TestPoint_Pad_1.0x1.0mm | 1
D7 | BZT52C12 | ~ | Diode_SMD:D_SOD-323 | 1 |  |  | BZT52C12
C30 | 3.3nF |  | Capacitor_SMD:C_0402_1005Metric | 1 |  |  | C1565
C50 | 3.3nF |  | Capacitor_SMD:C_0402_1005Metric | 1 |  |  | C1565
C9 | 0.1uF | ~ | Capacitor_SMD:C_0402_1005Metric | 1 |  |  | C1581
C11 | 0.1uF | ~ | Capacitor_SMD:C_0402_1005Metric | 1 |  |  | C1581
C15 | 0.1uF | ~ | Capacitor_SMD:C_0402_1005Metric | 1 |  |  | C1581
C16 | 0.1uF | ~ | Capacitor_SMD:C_0402_1005Metric | 1 |  |  | C1581
C48 | 0.1uF | ~ | Capacitor_SMD:C_0402_1005Metric | 1 |  |  | C1581
C52 | 0.1uF | ~ | Capacitor_SMD:C_0402_1005Metric | 1 |  |  | C1581
C19 | 1nF | ~ | Capacitor_SMD:C_0603_1608Metric | 1 |  |  | C1588
C20 | 1nF | ~ | Capacitor_SMD:C_0603_1608Metric | 1 |  |  | C1588
D10 | MOT_V_LED | ~ | LED_SMD:LED_0603_1608Metric | 1 |  |  | C2289
D14 | SERVO_V_LED | ~ | LED_SMD:LED_0603_1608Metric | 1 |  |  | C2289
D1 | CAM_STAT_LED | ~ | LED_SMD:LED_0603_1608Metric | 1 |  |  | C2290
D6 | BATT_PLUG_LED | ~ | LED_SMD:LED_0805_2012Metric | 1 |  |  | C2297
D9 | BATT_LED | ~ | LED_SMD:LED_0805_2012Metric | 1 |  |  | C2297
D11 | USB_LED | ~ | LED_SMD:LED_0805_2012Metric | 1 |  |  | C2297
D12 | 3V3_LED | ~ | LED_SMD:LED_0805_2012Metric | 1 |  |  | C2297
U7 | AMS1117-3.3 |  | Package_TO_SOT_SMD:SOT-223-3_TabPin2 | 1 |  |  | C6186
R21 | 200 | ~ | Resistor_SMD:R_0603_1608Metric | 1 |  |  | C8218
R26 | 200 | ~ | Resistor_SMD:R_0603_1608Metric | 1 |  |  | C8218
Q3 | 2N7002 | ${KIPRJMOD}/../../Datasheets/nmosfet_2N7002_DS.PDF | Package_TO_SOT_SMD:SOT-23 | 1 |  |  | C8545
D8 | SS34 |  | Diode_SMD:D_SMA | 1 |  |  | C8678
C22 | 2.2uF | ~ | Capacitor_SMD:C_0402_1005Metric | 1 |  |  | C12530
C4 | 0.1uF | ~ | Capacitor_SMD:C_0603_1608Metric | 1 |  |  | C14663
C10 | 0.1uF | ~ | Capacitor_SMD:C_0603_1608Metric | 1 |  |  | C14663
C12 | 0.1uF | ~ | Capacitor_SMD:C_0603_1608Metric | 1 |  |  | C14663
C14 | 0.1uF | ~ | Capacitor_SMD:C_0603_1608Metric | 1 |  |  | C14663
C17 | 0.1uF | ~ | Capacitor_SMD:C_0603_1608Metric | 1 |  |  | C14663
C18 | 0.1uF | ~ | Capacitor_SMD:C_0603_1608Metric | 1 |  |  | C14663
C28 | 0.1uF |  | Capacitor_SMD:C_0603_1608Metric | 1 |  |  | C14663
C33 | 0.1uF |  | Capacitor_SMD:C_0603_1608Metric | 1 |  |  | C14663
C34 | 0.1uF |  | Capacitor_SMD:C_0603_1608Metric | 1 |  |  | C14663
C36 | 0.1uF | ~ | Capacitor_SMD:C_0603_1608Metric | 1 |  |  | C14663
C39 | 0.1uF | ~ | Capacitor_SMD:C_0603_1608Metric | 1 |  |  | C14663
C41 | 0.1uF | ~ | Capacitor_SMD:C_0603_1608Metric | 1 |  |  | C14663
C43 | 0.1uF | ~ | Capacitor_SMD:C_0603_1608Metric | 1 |  |  | C14663
C44 | 0.1uF | ~ | Capacitor_SMD:C_0603_1608Metric | 1 |  |  | C14663
C45 | 0.1uF | ~ | Capacitor_SMD:C_0603_1608Metric | 1 |  |  | C14663
C46 | 0.1uF | ~ | Capacitor_SMD:C_0603_1608Metric | 1 |  |  | C14663
C21 | 10nF | ~ | Resistor_SMD:R_0402_1005Metric | 1 |  |  | C15195
C27 | 10nF | ~ | Capacitor_SMD:C_0603_1608Metric | 1 |  |  | C15195
C2 | 1uF | ~ | Capacitor_SMD:C_0603_1608Metric | 1 |  |  | C15849
C3 | 1uF | ~ | Capacitor_SMD:C_0603_1608Metric | 1 |  |  | C15849
C5 | 1uF | ~ | Capacitor_SMD:C_0603_1608Metric | 1 |  |  | C15849
C6 | 1uF | ~ | Capacitor_SMD:C_0603_1608Metric | 1 |  |  | C15849
C38 | 1uF | ~ | Capacitor_SMD:C_0603_1608Metric | 1 |  |  | C15849
C8 | 10uF | ~ | Capacitor_SMD:C_0805_2012Metric | 1 |  |  | C15850
C13 | 10uF | ~ | Capacitor_SMD:C_0805_2012Metric | 1 |  |  | C15850
C23 | 10uF | ~ | Capacitor_SMD:C_0805_2012Metric | 1 |  |  | C15850
C31 | 10uF | ~ | Capacitor_SMD:C_0805_2012Metric | 1 |  |  | C15850
C35 | 10uF | ~ | Capacitor_SMD:C_0805_2012Metric | 1 |  |  | C15850
C42 | 10uF | ~ | Capacitor_SMD:C_0805_2012Metric | 1 |  |  | C15850
C47 | 10uF | ~ | Capacitor_SMD:C_0805_2012Metric | 1 |  |  | C15850
C49 | 10uF | ~ | Capacitor_SMD:C_0805_2012Metric | 1 |  |  | C15850
Q1 | AO3400A |  | Package_TO_SOT_SMD:SOT-23 | 1 |  |  | C20917
R14 | 1.2k | ~ | Resistor_SMD:R_0603_1608Metric | 1 |  |  | C22765
R18 | 1.2k | ~ | Resistor_SMD:R_0603_1608Metric | 1 |  |  | C22765
R36 | 1.2k | ~ | Resistor_SMD:R_0603_1608Metric | 1 |  |  | C22765
R37 | 5.1k | ~ | Resistor_SMD:R_0603_1608Metric | 1 |  |  | C23186
R38 | 5.1k | ~ | Resistor_SMD:R_0603_1608Metric | 1 |  |  | C23186
R19 | 680 | ~ | Resistor_SMD:R_0603_1608Metric | 1 |  |  | C23228
R20 | 680 | ~ | Resistor_SMD:R_0603_1608Metric | 1 |  |  | C23228
R11 | 200 | ~ | Resistor_SMD:R_0402_1005Metric | 1 |  |  | C25087
R3 | 22 | ~ | Capacitor_SMD:C_0402_1005Metric | 1 |  |  | C25092
R4 | 22 | ~ | Capacitor_SMD:C_0402_1005Metric | 1 |  |  | C25092
R8 | 330 | ~ | Resistor_SMD:R_0402_1005Metric | 1 |  |  | C25104
R10 | 330 | ~ | Resistor_SMD:R_0402_1005Metric | 1 |  |  | C25104
R30 | 330 | ~ | Resistor_SMD:R_0402_1005Metric | 1 |  |  | C25104
R31 | 330 | ~ | Resistor_SMD:R_0402_1005Metric | 1 |  |  | C25104
R34 | 330 | ~ | Resistor_SMD:R_0402_1005Metric | 1 |  |  | C25104
R35 | 330 | ~ | Resistor_SMD:R_0402_1005Metric | 1 |  |  | C25104
R40 | 330 | ~ | Resistor_SMD:R_0402_1005Metric | 1 |  |  | C25104
R1 | 10k | ~ | Resistor_SMD:R_0402_1005Metric | 1 |  |  | C25744
R2 | 10k | ~ | Resistor_SMD:R_0402_1005Metric | 1 |  |  | C25744
R7 | 10k | ~ | Resistor_SMD:R_0402_1005Metric | 1 |  |  | C25744
R12 | 10k | ~ | Resistor_SMD:R_0402_1005Metric | 1 |  |  | C25744
R13 | 10k | ~ | Resistor_SMD:R_0402_1005Metric | 1 |  |  | C25744
R17 | 10k | ~ | Resistor_SMD:R_0402_1005Metric | 1 |  |  | C25744
R23 | 10k | ~ | Resistor_SMD:R_0402_1005Metric | 1 |  |  | C25744
R28 | 10k | ~ | Resistor_SMD:R_0402_1005Metric | 1 |  |  | C25744
R29 | 10k | ~ | Resistor_SMD:R_0402_1005Metric | 1 |  |  | C25744
R33 | 10k | ~ | Resistor_SMD:R_0402_1005Metric | 1 |  |  | C25744
R16 | 100k | ~ | Resistor_SMD:R_0603_1608Metric | 1 |  |  | C25803
R25 | 100k | ~ | Resistor_SMD:R_0603_1608Metric | 1 |  |  | C25803
R32 | 100k | ~ | Resistor_SMD:R_0603_1608Metric | 1 |  |  | C25803
R15 | 10k | ~ | Resistor_SMD:R_0603_1608Metric | 1 |  |  | C25804
R22 | 10k | ~ | Resistor_SMD:R_0603_1608Metric | 1 |  |  | C25804
R24 | 10k | ~ | Resistor_SMD:R_0603_1608Metric | 1 |  |  | C25804
R27 | 47k | ~ | Resistor_SMD:R_0603_1608Metric | 1 |  |  | C25819
R5 | 4.7k | ~ | Resistor_SMD:R_0402_1005Metric | 1 |  |  | C25900
R6 | 4.7k | ~ | Resistor_SMD:R_0402_1005Metric | 1 |  |  | C25900
C7 | 22uF | ~ | Capacitor_SMD:C_0805_2012Metric | 1 |  |  | C29277
C25 | 22uF | ~ | Capacitor_SMD:C_0805_2012Metric | 1 |  |  | C29277
C26 | 0.1uF | ~ | Capacitor_SMD:C_0805_2012Metric | 1 |  |  | C49678
C1 | 1uF | ~ | Capacitor_SMD:C_0402_1005Metric | 1 |  |  | C52923
D2 | DBG_LED | ~ | LED_SMD:LED_0603_1608Metric | 1 |  |  | C72038
R9 | 150 | ~ | Resistor_SMD:R_0402_1005Metric | 1 |  |  | C72038
D3 | WIFI_LED | ~ | LED_SMD:LED_0603_1608Metric | 1 |  |  | C72041
U3 | LP5907MFX-1.2 | http://www.ti.com/lit/ds/symlink/lp5907.pdf | Package_TO_SOT_SMD:SOT-23-5 | 1 |  |  | C73478
D13 | 1N4148W | ~ | Diode_SMD:D_SOD-123 | 1 |  |  | C81598
U9 | LSM6DSL | https://www.st.com/resource/en/datasheet/lsm6dsl.pdf | Package_LGA:LGA-14_3x2.5mm_P0.5mm_LayoutBorder3x4y | 1 |  |  | C94048
IC1 | HY2120-AB | https://datasheet.lcsc.com/szlcsc/HYCON-Tech-HY2120-AB_C168776.pdf | HY2120:SOT95P280X140-6N | 1 |  |  | C116509
FB1 | FerriteBead | ~ | Resistor_SMD:R_0805_2012Metric | 1 |  |  | C136227
U10 | TPS62143 | http://www.ti.com/lit/ds/symlink/TPS62140.pdf | Package_DFN_QFN:VQFN-16-1EP_3x3mm_P0.5mm_EP1.68x1.68mm_ThermalVias | 1 |  |  | C140242
U8 | DMP4065S-7 | ${KIPRJMOD}/../../Datasheets/pmosfet_DMP4065S-7_DS.pdf | Package_TO_SOT_SMD:SOT-23 | 1 |  |  | C182476
U2 | LP5907MFX-2.8 | http://www.ti.com/lit/ds/symlink/lp5907.pdf | Package_TO_SOT_SMD:SOT-23-5 | 1 |  |  | C186700
L1 | 10uH | https://www.vishay.com/docs/34295/ifsc-1515ah-01.pdf | IFSC1515AHER100M01:IND_IFSC_1515AH_VIS | 1 |  |  | C187450
J2 | CAM_HEADER | ~ | Connector_FFC-FPC:Hirose_FH12-24S-0.5SH_1x24-1MP_P0.50mm_Horizontal | 1 |  |  | C202112
U6 | TPS5405DR | https://www.ti.com/lit/ds/symlink/tps5405.pdf?HQS=dis-dk-null-digikeymode-dsf-pf-null-wwe&ts=1767031291543 | TPS5405DR:SOIC127P599X175-8N | 1 |  |  | C488409
U4 | DRV8833PW | http://www.ti.com/lit/ds/symlink/drv8833.pdf | Package_SO:TSSOP-16_4.4x5mm_P0.65mm | 1 |  |  | C544801
SW1 | SW_Boot | ~ | TACT_TS1185:SW_5-B-B-B-A_XKB | 1 |  |  | C561514
SW2 | SW_Reset | ~ | TACT_TS1185:SW_5-B-B-B-A_XKB | 1 |  |  | C561514
U5 | MCP23017_ML | http://ww1.microchip.com/downloads/en/DeviceDoc/20001952C.pdf | Package_DFN_QFN:QFN-28-1EP_6x6mm_P0.65mm_EP4.25x4.25mm | 1 |  |  | C629439
Q4 | FS8205A | http://www.techpublic.com.tw/pdf/FS8205A.pdf | F58205A:SOT95P280X125-6N | 1 |  |  | C908265
UE1 | ID_LM66100DCKR | https://www.ti.com/general/docs/suppproductinfo.tsp?distId=10 | Package_TO_SOT_SMD:SOT-363_SC-70-6 | 1 |  |  | C2869734
UE2 | ID_LM66100DCKR | https://www.ti.com/general/docs/suppproductinfo.tsp?distId=10 | Package_TO_SOT_SMD:SOT-363_SC-70-6 | 1 |  |  | C2869734
U1 | ESP32-S3-WROOM-1U-N8R8 | https://documentation.espressif.com/esp32-s3-wroom-1_wroom-1u_datasheet_en.pdf | RF_Module:ESP32-S3-WROOM-1U | 1 |  |  | C2980300
J1 | USB_C_CONN | ${KIPRJMOD}/../../Datasheets/USBconn_DS.pdf | Connector_USB:USB_C_Receptacle_G-Switch_GT-USB-7010ASV | 1 |  |  | C5178541
L2 | 2.2uH | ~ | Inductor_SMD_Wurth:L_Wurth_WE-LQSH-4020 | 1 |  |  | C5521727
J5 | I2C_JUMPER | ~ | Connector_PinHeader_1.27mm:PinHeader_1x04_P1.27mm_Vertical | 1 |  |  | C6333215
J6 | I2C_JUMPER | ~ | Connector_PinHeader_1.27mm:PinHeader_1x04_P1.27mm_Vertical | 1 |  |  | C6333215
Q2 | SI2393DS | http://www.vishay.com/docs/66709/si2319cd.pdf | Package_TO_SOT_SMD:SOT-23 | 1 |  |  | C41348109
C29 | 22uF | ~ | Capacitor_SMD:C_1206_3216Metric | 1 |  |  | C49326779
C32 | 22uF | ~ | Capacitor_SMD:C_1206_3216Metric | 1 |  |  | C49326779
C37 | 22uF | ~ | Capacitor_SMD:C_1206_3216Metric | 1 |  |  | C49326779
C51 | 22uF | ~ | Capacitor_SMD:C_1206_3216Metric | 1 |  |  | C49326779

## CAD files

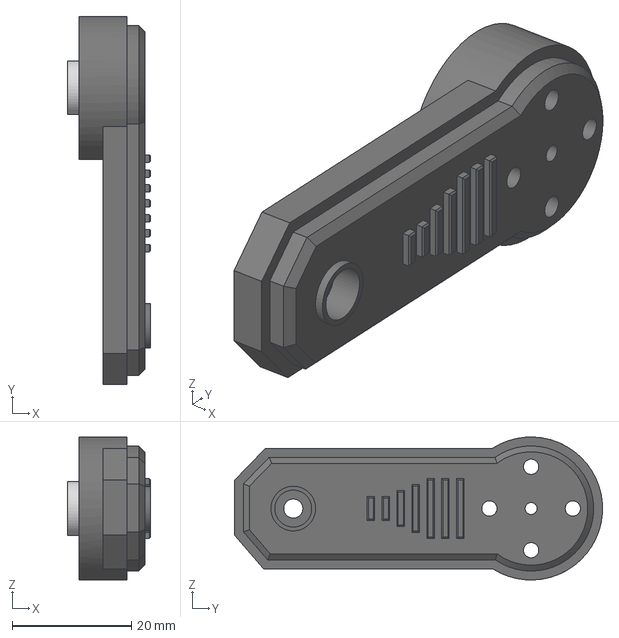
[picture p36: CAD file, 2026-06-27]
cad/body/assemblies/mounting_arm (Assembly).step
14.0 x 61.7 x 24.0 mm
[3879] Servo Motor Horn for MG995 MG996 Series Motor SunRobotics_in_f ron
mounting_arm

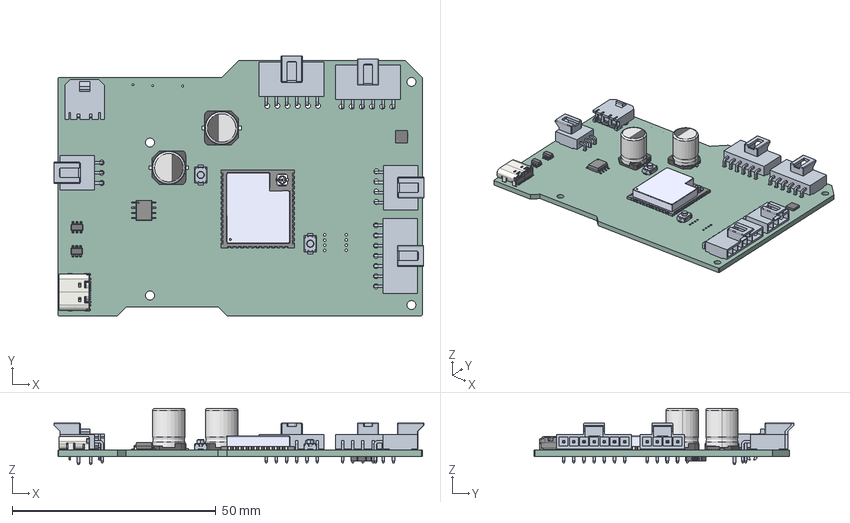
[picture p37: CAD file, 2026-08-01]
cad/board/board.step
90.8 x 63.8 x 13.9 mm
EEE-1EA101P x 2
ESP32-S3-WROOM-1U-N16R8
USB_C_Receptacle_16P_TopMnt_Horizontal_GCT_USB4105-xx-A
SOT_23_6 x 2
TS-1185-X-B-A-A x 2
QFN-16-1EP_3x3mm_P0.5mm_EP1.7x1.7mm
SOIC_standard
SMT-0540-S-R
penguin_PCB

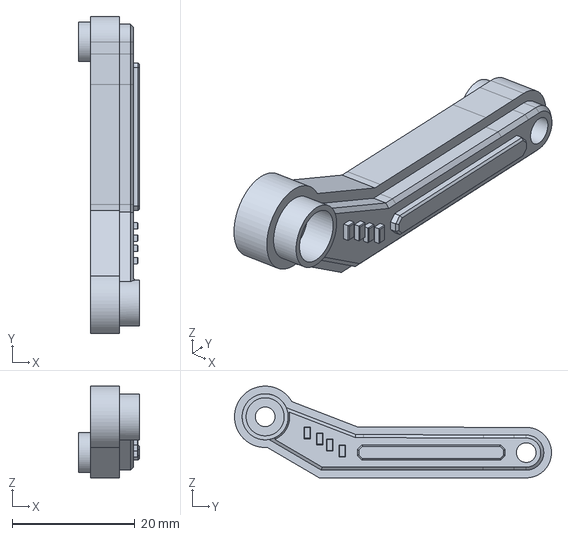
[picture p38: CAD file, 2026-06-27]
cad/body/legs/pivot_arm_L.step
10.0 x 51.6 x 14.9 mm

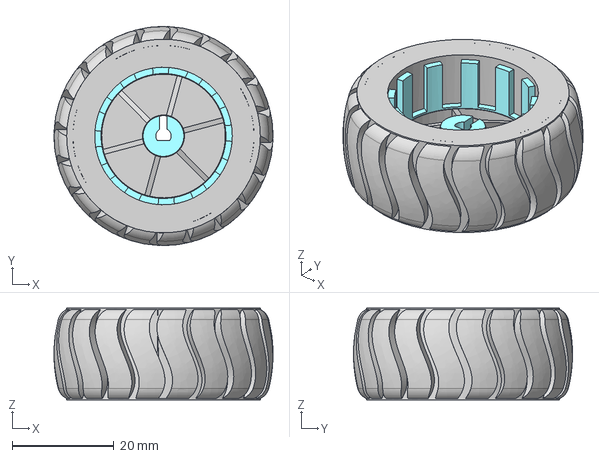
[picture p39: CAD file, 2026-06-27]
cad/body/misc/extern/RC wheel.step
43.0 x 43.0 x 18.0 mm
Housing
Hub

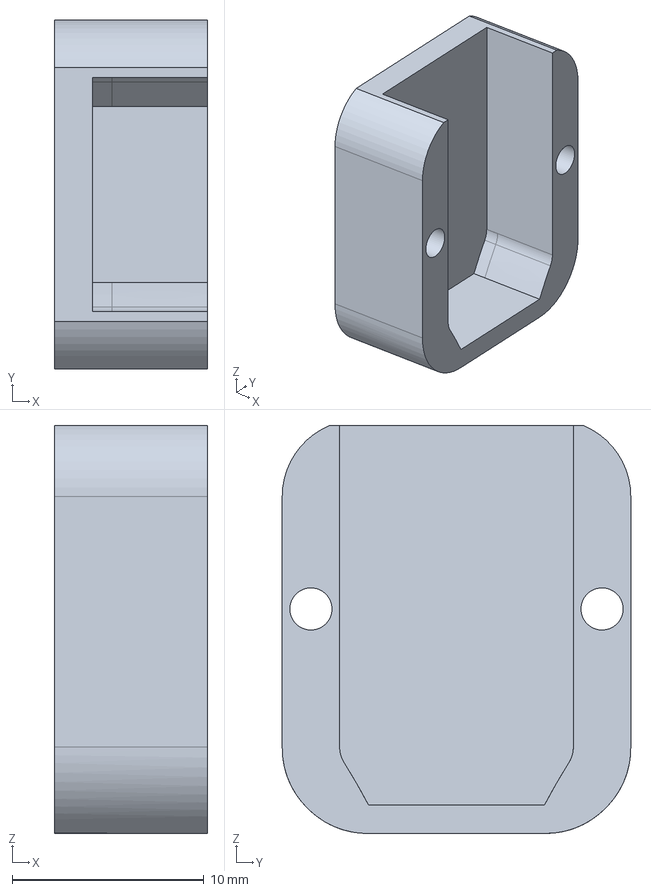
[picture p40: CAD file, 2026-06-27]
cad/body/misc/U_Channel_Lock.step
8.00 x 18.2 x 21.3 mm

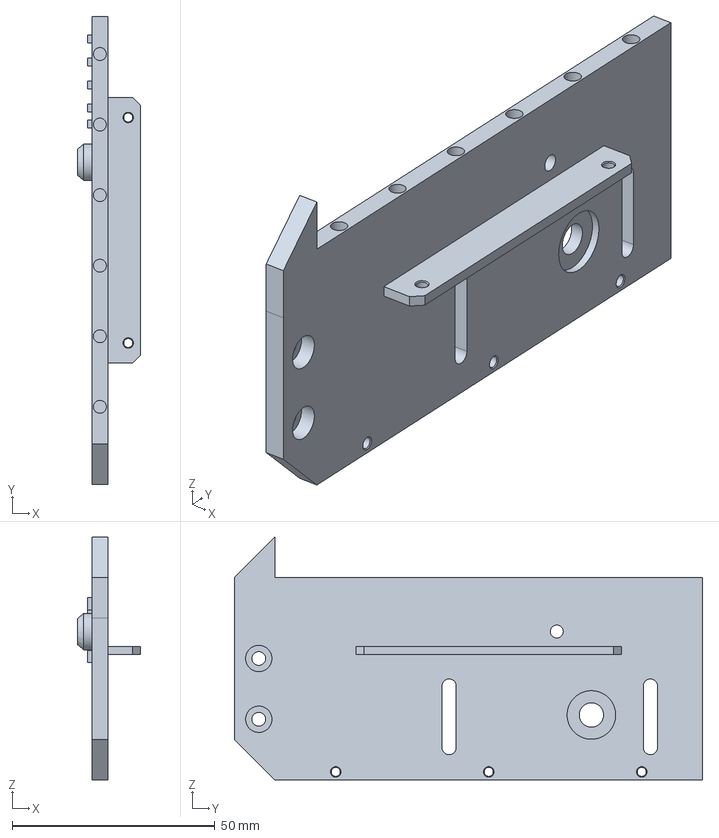
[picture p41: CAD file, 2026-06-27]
cad/body/torso/side_wall_L.step
15.5 x 115.6 x 60.0 mm

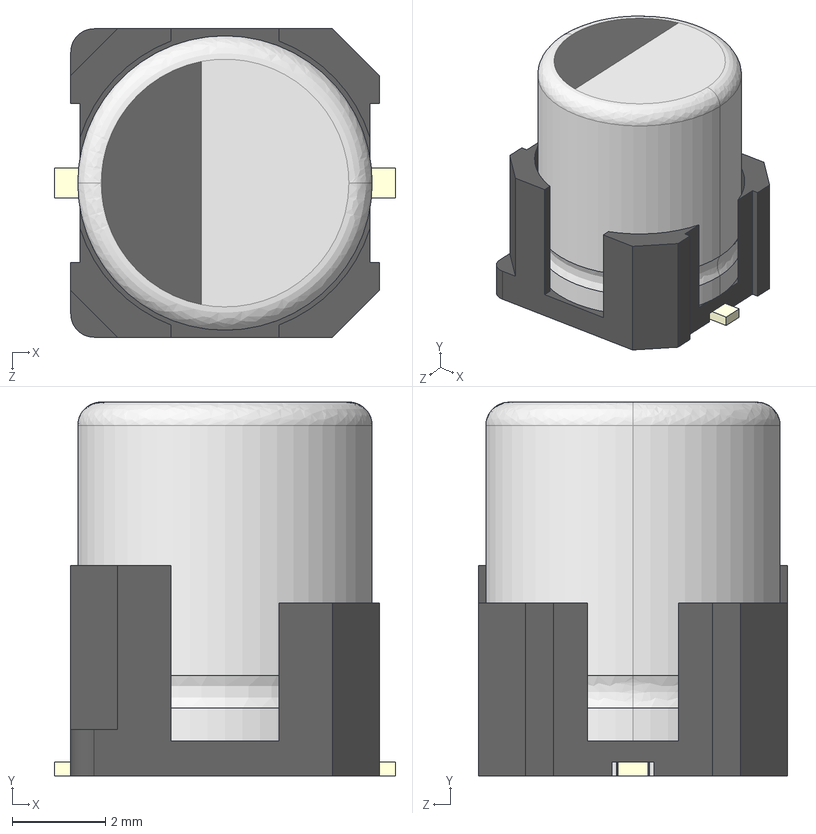
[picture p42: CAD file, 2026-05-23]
controller/models/EEHZK1V101XV.step
7.30 x 8.00 x 6.60 mm

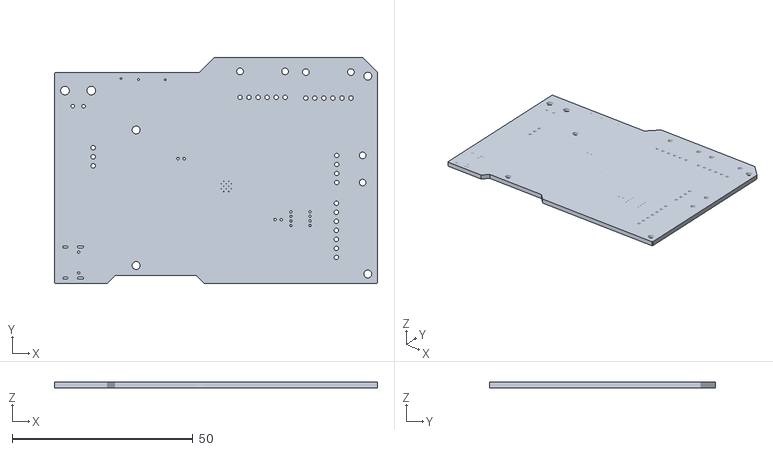
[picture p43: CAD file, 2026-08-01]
dashboard/public/models/board.stl
89.5 x 62.6 x 1.60

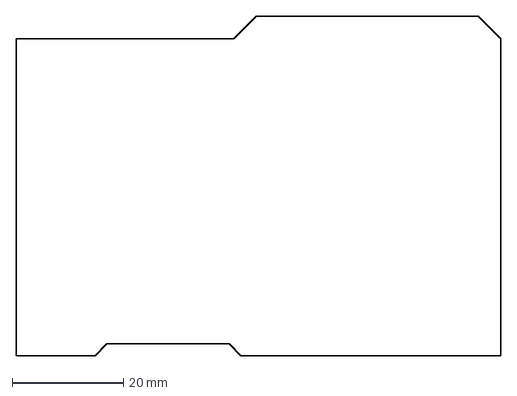
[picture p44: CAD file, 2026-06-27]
cad/board/controller_board_outline.dxf
87.3 x 61.1 mm

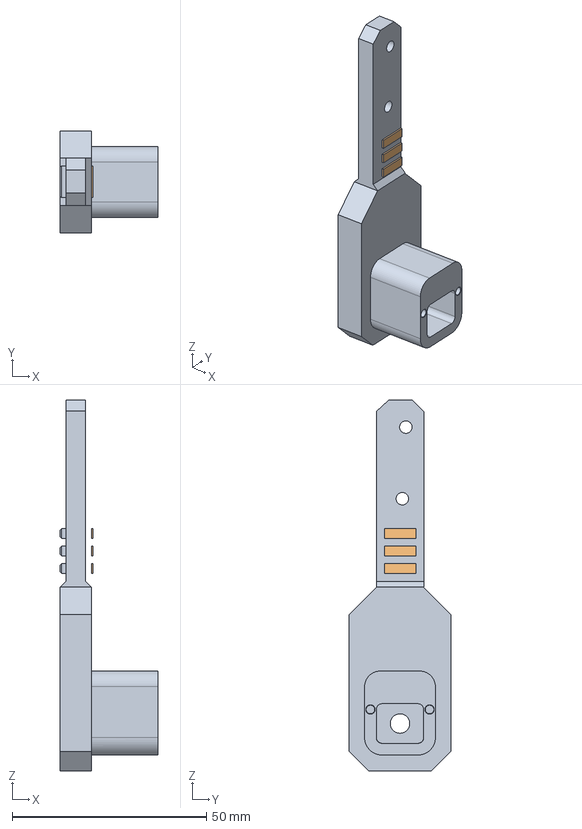
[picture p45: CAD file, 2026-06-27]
cad/body/legs/leg_L.step
25.1 x 26.1 x 95.4 mm

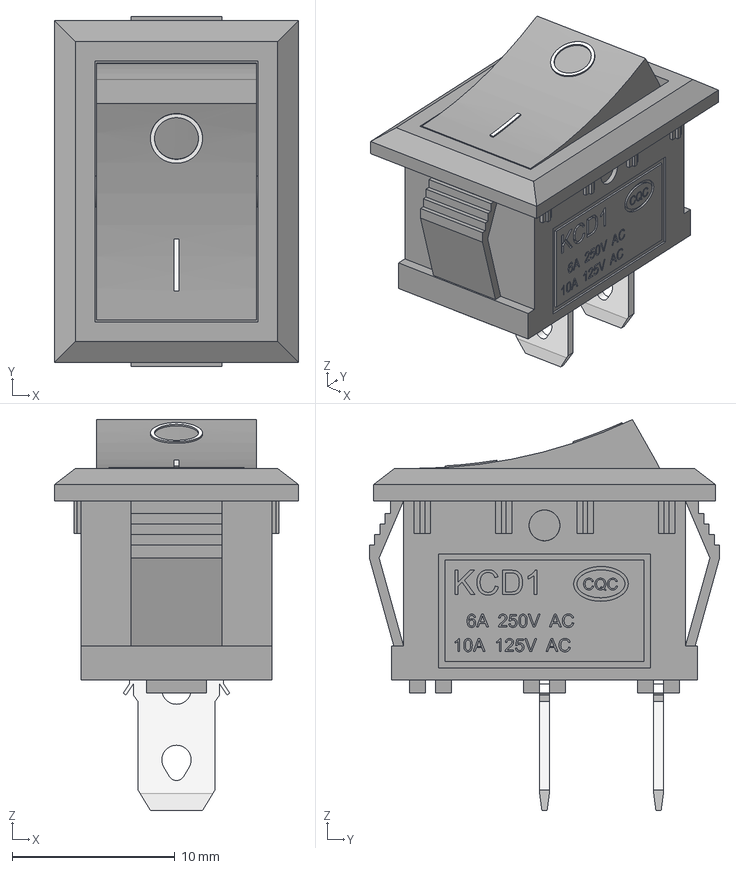
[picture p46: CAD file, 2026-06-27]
cad/body/misc/extern/kcd1_a.step
15.0 x 21.5 x 24.0 mm
Blade_001
Blade_002
Base_w_text
knob001

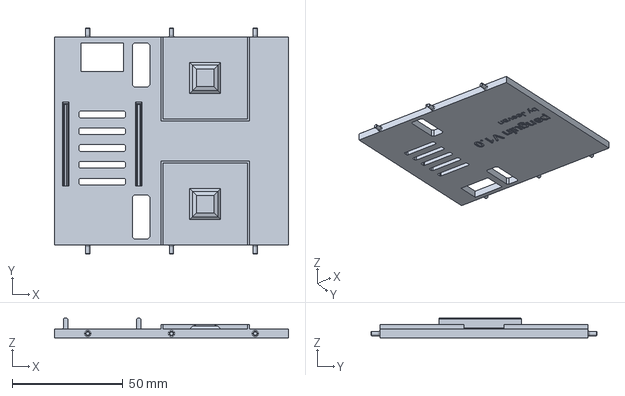
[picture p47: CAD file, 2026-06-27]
cad/body/torso/bottom_plate.step
105.6 x 102.0 x 9.00 mm

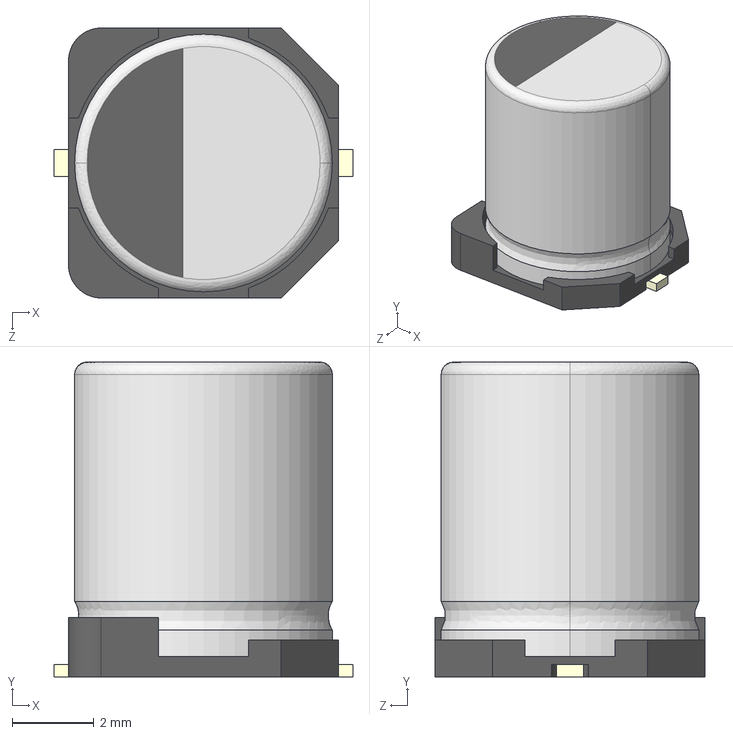
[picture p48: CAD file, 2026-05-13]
controller/models/EEH-ZK1V101XP.step
7.30 x 7.70 x 6.60 mm

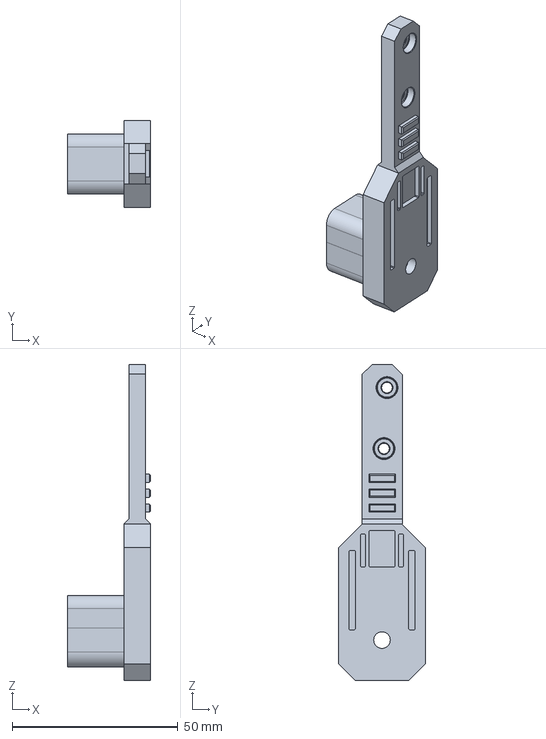
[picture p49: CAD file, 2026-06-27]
cad/body/legs/leg_R.step
25.1 x 26.1 x 95.4 mm

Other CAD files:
cad/body/misc/extern/[3879] Servo Motor Horn for MG995 MG996 Series Motor SunRobotics_in_fron.step
cad/body/torso/side_wall_R.step
cad/body/legs/pivot_arm_R.step
cad/body/torso/nose.step
cad/body/legs/mounting_arm.step
cad/body/torso/mid_plate.step
cad/body/torso/roof.step
cad/body/torso/stern.step
controller/models/1053131102.step
controller/models/1053131107.stp
controller/models/1053131203.stp
controller/models/1053131204.stp
controller/models/1053131206.step
controller/models/436500204.step
controller/models/EEEFK1V101P.step
controller/models/ESP32-S3-WROOM-1U-N8R8--3DModel-STEP-56544.STEP
controller/models/FS8205A.stp
controller/models/HY2120-AB.stp
controller/models/SMT-0540-S-R.step
controller/models/STM32F411CEU6.step
controller/models/TPS5405DR.step
controller/models/TS-3025-A-A-B.stp
controller/models/ts-1185-x-b-a-a.stp

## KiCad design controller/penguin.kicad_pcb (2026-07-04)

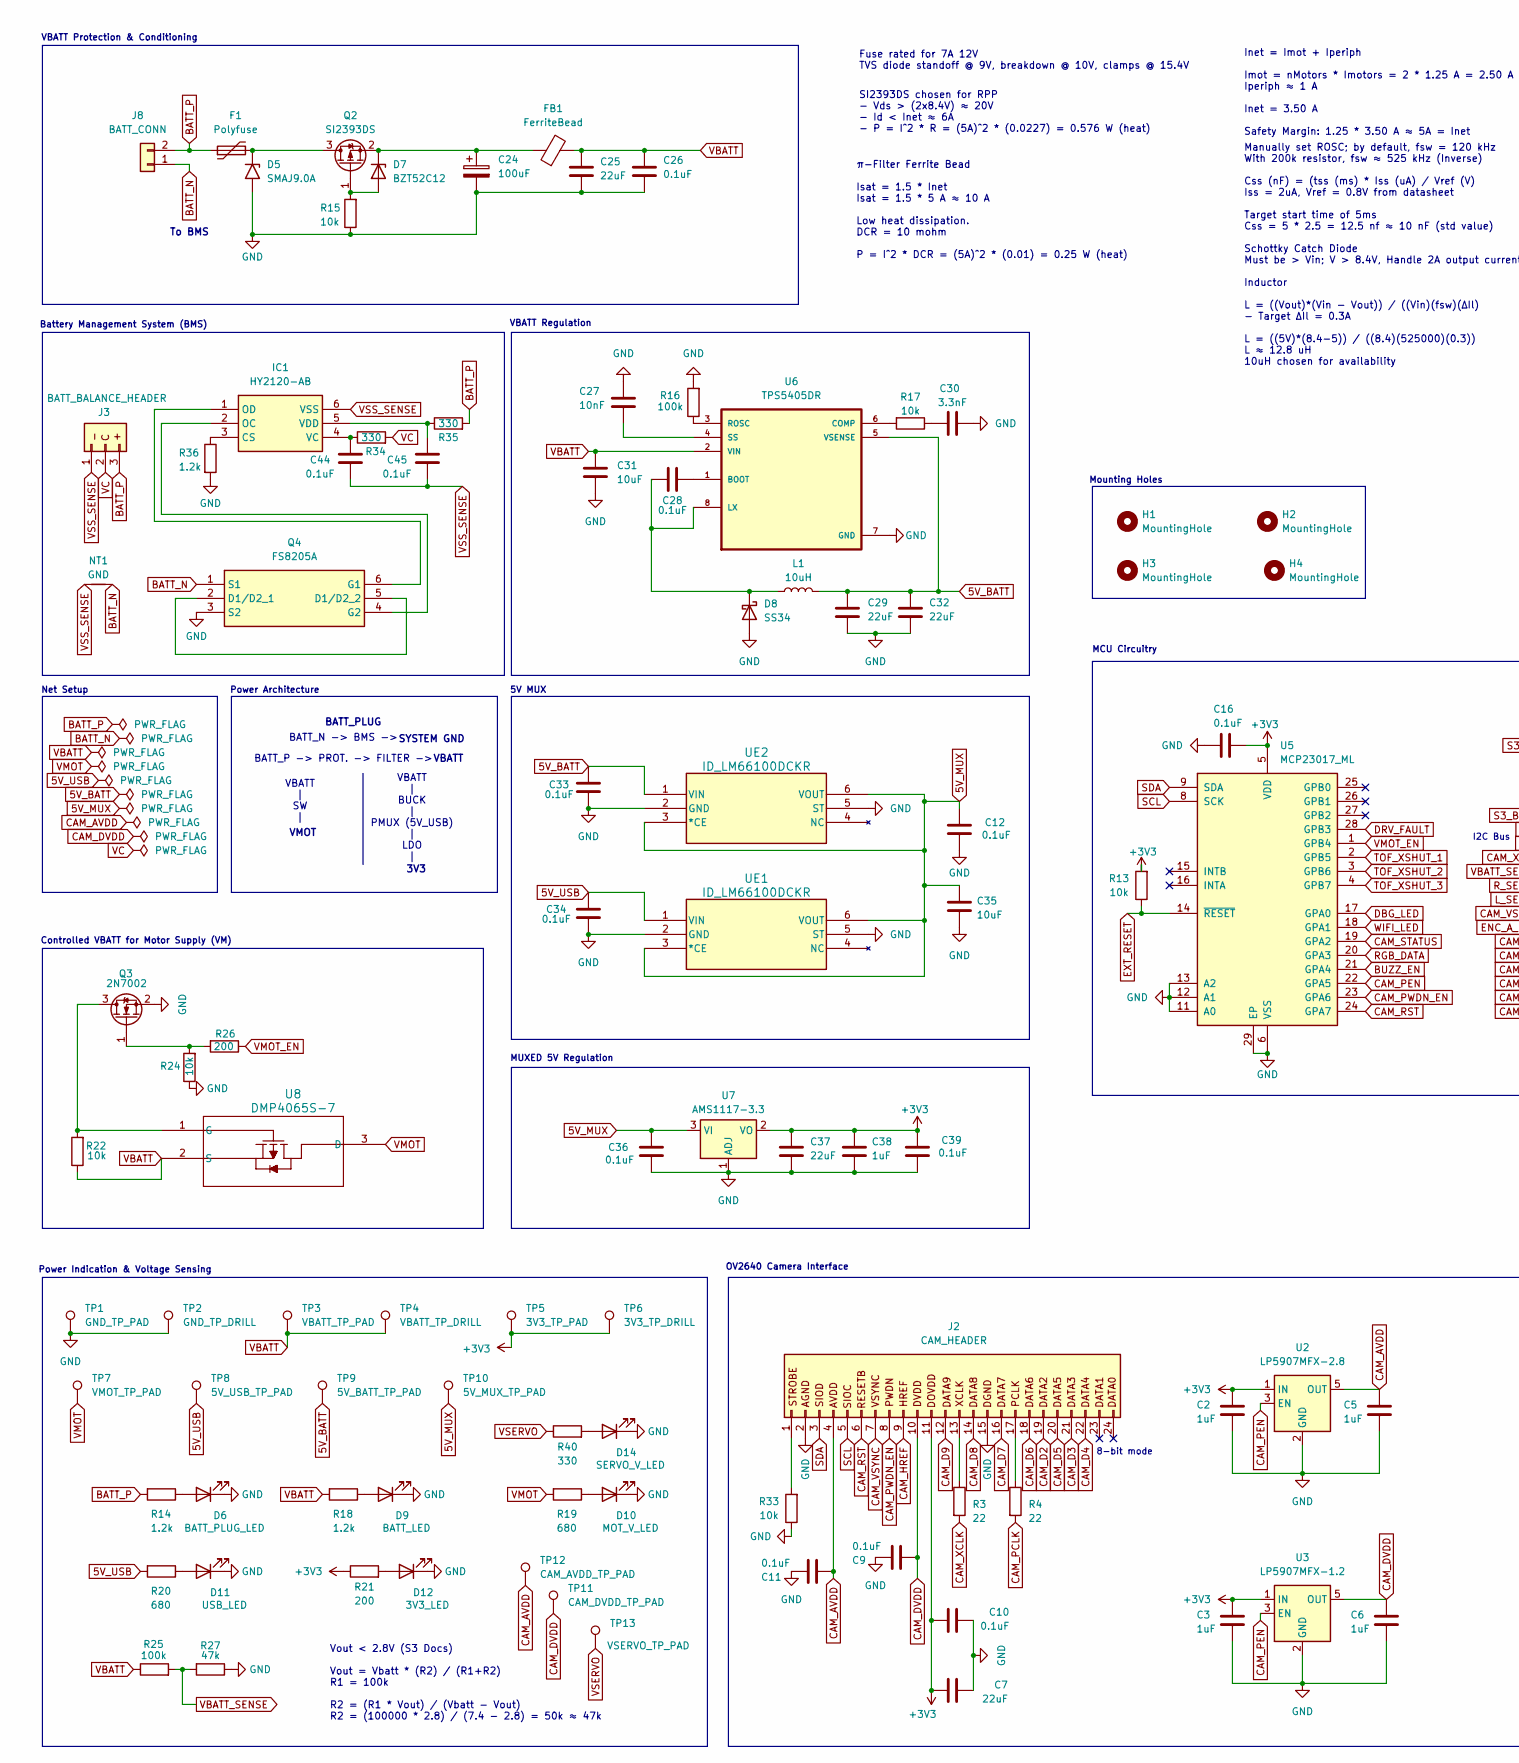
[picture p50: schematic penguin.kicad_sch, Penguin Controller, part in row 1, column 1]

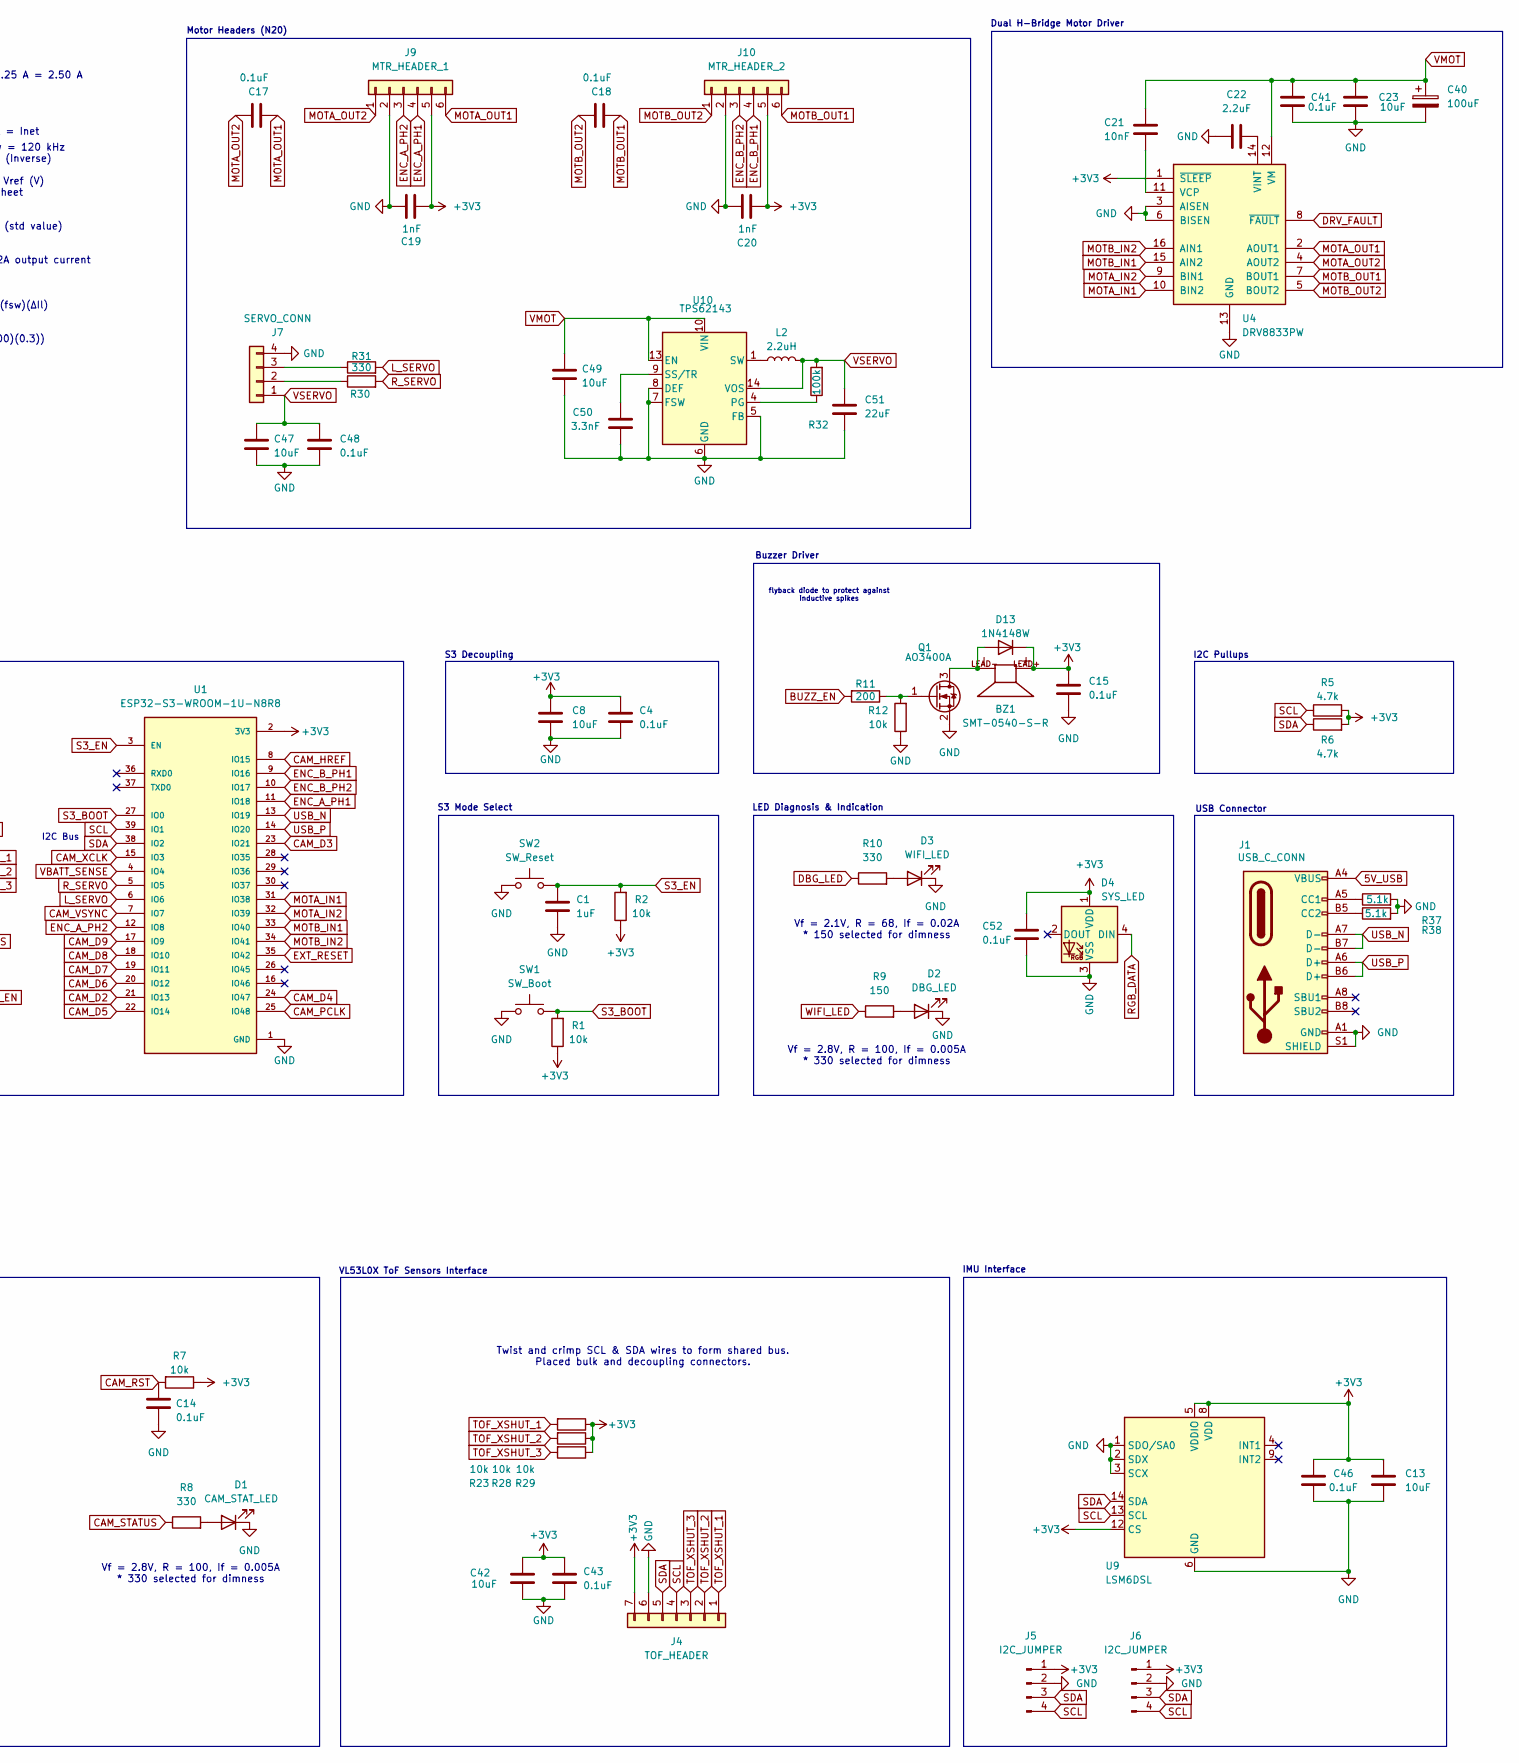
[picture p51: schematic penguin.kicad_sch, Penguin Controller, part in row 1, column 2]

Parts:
BZ1: SMT-0540-S-R; XDCR_SMT-0540-S-R; PARTREV D
C1: 1uF; C_0402_1005Metric; LCSC C52923
C2, C3, C5, C6, C38: 1uF; C_0603_1608Metric; LCSC C15849
C4, C10, C12, C14, C17, C18, C28, C33, C34, C36, C39, C41, C43, C44, C45, C46: 0.1uF; C_0603_1608Metric; LCSC C14663
C7, C25: 22uF; C_0805_2012Metric; LCSC C29277
C8, C13, C23, C31, C35, C42, C47, C49: 10uF; C_0805_2012Metric; LCSC C15850
C9, C11, C15, C16, C48, C52: 0.1uF; C_0402_1005Metric; LCSC C1581
C19, C20: 1nF; C_0603_1608Metric; LCSC C1588
C21: 10nF; C_0402_1005Metric; LCSC C15195
C22: 2.2uF; C_0402_1005Metric; LCSC C12530
C24, C40: 100uF; CAP_EEEFK1V101P; Digikey ZK1V101XV
C26: 0.1uF; C_0805_2012Metric; LCSC C49678
C27: 10nF; C_0603_1608Metric; LCSC C15195
C29, C32, C37, C51: 22uF; C_1206_3216Metric; LCSC C49326779
C30, C50: 3.3nF; C_0402_1005Metric; LCSC C1536
D1: CAM_STAT_LED; LED_0603_1608Metric; LCSC C2290
D2: DBG_LED; LED_0603_1608Metric; LCSC C72038
D3: WIFI_LED; LED_0603_1608Metric; LCSC C72041
D4: SYS_LED; LED_WS2812B-Mini_PLCC4_3.5x3.5mm; Digikey 1568-COM-16347CT-ND
D5: SMAJ9.0A; D_SMA; Digikey SMAJ9.0ABTR-ND
D6: BATT_PLUG_LED; LED_0805_2012Metric; LCSC C2297
D7: BZT52C12; D_SOD-323; LCSC BZT52C12
D8: SS34; D_SMA; LCSC C8678
D9: BATT_LED; LED_0805_2012Metric; LCSC C2297
D10: MOT_V_LED; LED_0603_1608Metric; LCSC C2289
D11: USB_LED; LED_0805_2012Metric; LCSC C2297
D12: 3V3_LED; LED_0805_2012Metric; LCSC C2297
D13: 1N4148W; D_SOD-123; LCSC C81598
D14: SERVO_V_LED; LED_0603_1608Metric; LCSC C2289
F1: Polyfuse; Fuse_1210_3225Metric_Pad1.42x2.65mm_HandSolder; Digikey F8137TR-ND
FB1: FerriteBead; R_0805_2012Metric; LCSC C136227
H1, H2, H3, H4: MountingHole; MountingHole_2.2mm_M2
IC1: HY2120-AB; SOT95P280X140-6N; LCSC C116509
J1: USB_C_CONN; USB_C_Receptacle_G-Switch_GT-USB-7010ASV; LCSC C5178541
J2: CAM_HEADER; Hirose_FH12-24S-0.5SH_1x24-1MP_P0.50mm_Horizontal; LCSC C202112
J3: BATT_BALANCE_HEADER; CONN_SD-105313-100_03_MOL; Digikey WM14973-ND
J4: TOF_HEADER; CONN_SD-105313-100_07_MOL; Digikey WM16898-ND
J5, J6: I2C_JUMPER; PinHeader_1x04_P1.27mm_Vertical; LCSC C6333215
J7: SERVO_CONN; CONN_SD-105313-100_04_MOL; DigiKey WM14974-ND
J8: BATT_CONN; MOLEX_436500204; Digikey WM1875-ND
J9: MTR_HEADER_1; CONN_SD-105313-100_06_MOL; Digikey WM16893-ND
J10: MTR_HEADER_2; CONN_SD-105313-100_06_MOL; Digikey WM16893-ND
L1: 10uH; IND_IFSC_1515AH_VIS; LCSC C187450
L2: 2.2uH; L_Wurth_WE-LQSH-4020; LCSC C5521727
NT1: GND; NetTie-2_SMD_Pad0.5mm
Q1: AO3400A; SOT-23; LCSC C20917
Q2: SI2393DS; SOT-23; LCSC C41348109
Q3: 2N7002; SOT-23; LCSC C8545
Q4: FS8205A; SOT95P280X125-6N; LCSC C908265
R1, R2, R7, R12, R13, R17, R23, R28, R29, R33: 10k; R_0402_1005Metric; LCSC C25744
R3, R4: 22; C_0402_1005Metric; LCSC C25092
R5, R6: 4.7k; R_0402_1005Metric; LCSC C25900
R8, R10, R30, R31, R34, R35, R40: 330; R_0402_1005Metric; LCSC C25104
R9: 150; R_0402_1005Metric; LCSC C72038
R11: 200; R_0402_1005Metric; LCSC C25087
R14, R18, R36: 1.2k; R_0603_1608Metric; LCSC C22765
R15, R22, R24: 10k; R_0603_1608Metric; LCSC C25804
R16, R25, R32: 100k; R_0603_1608Metric; LCSC C25803
R19, R20: 680; R_0603_1608Metric; LCSC C23228
R21, R26: 200; R_0603_1608Metric; LCSC C8218
R27: 47k; R_0603_1608Metric; LCSC C25819
R37, R38: 5.1k; R_0603_1608Metric; LCSC C23186
SW1: SW_Boot; SW_5-B-B-B-A_XKB; LCSC C561514
SW2: SW_Reset; SW_5-B-B-B-A_XKB; LCSC C561514
TP1: GND_TP_PAD; TestPoint_Pad_1.5x1.5mm
TP2: GND_TP_DRILL; TestPoint_THTPad_D1.0mm_Drill0.5mm
TP3: VBATT_TP_PAD; TestPoint_Pad_1.5x1.5mm
TP4: VBATT_TP_DRILL; TestPoint_THTPad_D1.0mm_Drill0.5mm
TP5: 3V3_TP_PAD; TestPoint_Pad_1.5x1.5mm
TP6: 3V3_TP_DRILL; TestPoint_THTPad_D1.0mm_Drill0.5mm
TP7: VMOT_TP_PAD; TestPoint_Pad_1.0x1.0mm
TP8: 5V_USB_TP_PAD; TestPoint_Pad_1.0x1.0mm
TP9: 5V_BATT_TP_PAD; TestPoint_Pad_1.0x1.0mm
TP10: 5V_MUX_TP_PAD; TestPoint_Pad_1.0x1.0mm
TP11: CAM_DVDD_TP_PAD; TestPoint_Pad_1.0x1.0mm
TP12: CAM_AVDD_TP_PAD; TestPoint_Pad_1.0x1.0mm
TP13: VSERVO_TP_PAD; TestPoint_Pad_1.0x1.0mm
U1: ESP32-S3-WROOM-1U-N8R8; ESP32-S3-WROOM-1U; LCSC C2980300
U2: LP5907MFX-2.8; SOT-23-5; LCSC C186700
U3: LP5907MFX-1.2; SOT-23-5; LCSC C73478
U4: DRV8833PW; TSSOP-16_4.4x5mm_P0.65mm; LCSC C544801
U5: MCP23017_ML; QFN-28-1EP_6x6mm_P0.65mm_EP4.25x4.25mm; LCSC C629439
U6: TPS5405DR; SOIC127P599X175-8N; LCSC C488409
U7: AMS1117-3.3; SOT-223-3_TabPin2; LCSC C6186
U8: DMP4065S-7; SOT-23; LCSC C182476
U9: LSM6DSL; LGA-14_3x2.5mm_P0.5mm_LayoutBorder3x4y; LCSC C94048
U10: TPS62143; VQFN-16-1EP_3x3mm_P0.5mm_EP1.68x1.68mm_ThermalVias; LCSC C140242
UE1, UE2: ID_LM66100DCKR; SOT-363_SC-70-6; LCSC C2869734

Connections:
5V_BATT: C29.1, C32.1, C33.2, L1.2, TP9.1, U6.5 (VSENSE), UE2.1 (VIN)
5V_MUX: C12.2, C35.2, C36.2, TP10.1, U7.3 (VI), UE1.3 (*CE), UE1.6 (VOUT), UE2.3 (*CE), UE2.6 (VOUT)
5V_USB: C34.1, J1.A4 (VBUS), J1.A9 (VBUS), J1.B4 (VBUS), J1.B9 (VBUS), R20.2, TP8.1, UE1.1 (VIN)
+3V3: BZ1.LEAD+, C2.1, C3.1, C4.1, C7.1, C8.1, C10.1, C13.1, C15.1, C16.1, C19.2, C20.2, C37.1, C38.1, C39.2, C42.1, C43.1, C46.2, C52.1, D4.1 (VDD), D13.1 (K), J2.11, J4.7, J5.1, J6.1, J9.5, J10.5, R1.1, R2.1, R5.2, R6.2, R7.1, R13.2, R21.1, R23.1, R28.1, R29.1, TP5.1, TP6.1, U1.2 (3V3), U2.1 (IN), U3.1 (IN), U4.1 (~SLEEP), U5.5 (VDD), U7.2 (VO), U9.5 (VDDIO), U9.8 (VDD), U9.12 (CS)
BATT_N: J8.1, NT1.2, Q4.1 (S1)
BATT_P: F1.1, J3.3, J8.2, R14.2, R35.2
BUZZ_EN: R11.2, U5.21 (GPA4)
CAM_AVDD: C5.1, C11.1, J2.4, TP12.1, U2.5 (OUT)
CAM_D2: J2.19, U1.21 (IO13)
CAM_D3: J2.21, U1.23 (IO21)
CAM_D4: J2.22, U1.24 (IO47)
CAM_D5: J2.20, U1.22 (IO14)
CAM_D6: J2.18, U1.20 (IO12)
CAM_D7: J2.16, U1.19 (IO11)
CAM_D8: J2.14, U1.18 (IO10)
CAM_D9: J2.12, U1.17 (IO9)
CAM_DVDD: C6.1, C9.1, J2.10, TP11.1, U3.5 (OUT)
CAM_HREF: J2.9, U1.8 (IO15)
CAM_PCLK: R4.2, U1.25 (IO48)
CAM_PEN: U2.3 (EN), U3.3 (EN), U5.22 (GPA5)
CAM_PWDN_EN: J2.8, U5.23 (GPA6)
CAM_RST: C14.1, J2.6, R7.2, U5.24 (GPA7)
CAM_STATUS: R8.1, U5.19 (GPA2)
CAM_VSYNC: J2.7, U1.7 (IO7)
CAM_XCLK: R3.2, U1.15 (IO3)
DBG_LED: R10.1, U5.17 (GPA0)
DRV_FAULT: U4.8 (~FAULT), U5.28 (GPB3)
ENC_A_PH1: J9.4, U1.11 (IO18)
ENC_A_PH2: J9.3, U1.12 (IO8)
ENC_B_PH1: J10.4, U1.9 (IO16)
ENC_B_PH2: J10.3, U1.10 (IO17)
EXT_RESET: R13.1, U1.35 (IO42), U5.14 (~RESET)
GND: C1.2, C2.2, C3.2, C4.2, C5.2, C6.2, C7.2, C8.2, C9.2, C10.2, C11.2, C12.1, C13.2, C14.2, C15.2, C16.2, C19.1, C20.1, C22.1, C23.2, C24.2, C25.2, C26.2, C27.1, C29.2, C30.2, C31.2, C32.2, C33.1, C34.2, C35.1, C36.1, C37.2, C38.2, C39.1, C40.2, C41.1, C42.2, C43.2, C46.1, C47.1, C48.2, C49.1, C50.1, C51.2, C52.2, D1.1 (K), D2.1 (K), D3.1 (K), D4.3 (VSS), D5.2 (A2), D6.1 (K), D8.2 (A), D9.1 (K), D10.1 (K), D11.1 (K), D12.1 (K), D14.1 (K), J1.A1 (GND), J1.A12 (GND), J1.B1 (GND), J1.B12 (GND), J1.S1 (SHIELD), J2.2, J2.15, J4.6, J5.2, J6.2, J7.4, J9.2, J10.2, Q1.2 (S), Q3.2 (S), Q4.3 (S2), R12.1, R15.1, R16.2, R24.1, R27.1, R33.1, R36.2, R37.2, R38.2, SW1.1, SW2.1, TP1.1, TP2.1, U1.1 (GND), U1.40 (GND), U1.41_1 (GND), U1.41_2 (GND), U1.41_3 (GND), U1.41_4 (GND), U1.41_5 (GND), U1.41_6 (GND), U1.41_7 (GND), U1.41_8 (GND), U1.41_9 (GND), U2.2 (GND), U3.2 (GND), U4.3 (AISEN), U4.6 (BISEN), U4.13 (GND), U5.6 (VSS), U5.11 (A0), U5.12 (A1), U5.13 (A2), U5.29 (EP), U6.7 (GND), U7.1 (ADJ), U9.1 (SDO/SA0), U9.2 (SDX), U9.3 (SCX), U9.6 (GND), U9.7 (GND), U10.5 (FB), U10.6 (GND), U10.7 (FSW), U10.8 (DEF), U10.15 (GND), U10.16 (GND), U10.17 (GND), UE1.2 (GND), UE1.5 (ST), UE2.2 (GND), UE2.5 (ST)
L_SERVO: R31.2, U1.6 (IO6)
MOTA_IN1: U1.31 (IO38), U4.10 (BIN2)
MOTA_IN2: U1.32 (IO39), U4.9 (BIN1)
MOTA_OUT1: C17.2, J9.6, U4.2 (AOUT1)
MOTA_OUT2: C17.1, J9.1, U4.4 (AOUT2)
MOTB_IN1: U1.33 (IO40), U4.15 (AIN2)
MOTB_IN2: U1.34 (IO41), U4.16 (AIN1)
MOTB_OUT1: C18.2, J10.6, U4.7 (BOUT1)
MOTB_OUT2: C18.1, J10.1, U4.5 (BOUT2)
unnamed: C30.1, R17.1
unnamed: D1.2 (A), R8.2
unnamed: D2.2 (A), R9.2
unnamed: D3.2 (A), R10.2
unnamed: D5.1 (A1), F1.2, Q2.3 (D)
unnamed: D6.2 (A), R14.1
unnamed: D7.2 (A), Q2.1 (G), R15.2
unnamed: C24.1, D7.1 (K), FB1.1, Q2.2 (S)
unnamed: C28.1, D8.1 (K), L1.1, U6.8 (LX)
unnamed: D9.2 (A), R18.1
unnamed: D10.2 (A), R19.1
unnamed: D11.2 (A), R20.1
unnamed: D12.2 (A), R21.2
unnamed: BZ1.LEAD-, D13.2 (A), Q1.3 (D)
unnamed: D14.2 (A), R40.2
unnamed: IC1.3 (CS), R36.1
unnamed: IC1.2 (OC), Q4.4 (G2)
unnamed: IC1.1 (OD), Q4.6 (G1)
unnamed: C44.2, IC1.4 (VC), R34.1
unnamed: C45.2, IC1.5 (VDD), R35.1
unnamed: J1.A5 (CC1), R37.1
unnamed: J1.B5 (CC2), R38.1
unnamed: J2.1, R33.2
unnamed: J2.13, R3.1
unnamed: J2.17, R4.1
unnamed: J7.2, R30.1
unnamed: J7.3, R31.1
unnamed: L2.1, U10.1 (SW), U10.2 (SW), U10.3 (SW)
unnamed: Q1.1 (G), R11.1, R12.2
unnamed: Q3.3 (D), R22.2, U8.1 (G)
unnamed: Q3.1 (G), R24.2, R26.2
unnamed: Q4.2 (D1/D2_1), Q4.5 (D1/D2_2)
unnamed: C21.2, U4.11 (VCP)
unnamed: C22.2, U4.14 (VINT)
unnamed: C28.2, U6.1 (BOOT)
unnamed: R17.2, U6.6 (COMP)
unnamed: R16.1, U6.3 (ROSC)
unnamed: C27.2, U6.4 (SS)
unnamed: R32.1, U10.4 (PG)
unnamed: C50.2, U10.9 (SS/TR)
RGB_DATA: D4.4 (DIN), U5.20 (GPA3)
R_SERVO: R30.2, U1.5 (IO5)
S3_BOOT: R1.2, SW1.2, U1.27 (IO0)
S3_EN: C1.1, R2.2, SW2.2, U1.3 (EN)
SCL: J2.5, J4.4, J5.4, J6.4, R5.1, U1.39 (IO1), U5.8 (SCK), U9.13 (SCL)
SDA: J2.3, J4.5, J5.3, J6.3, R6.1, U1.38 (IO2), U5.9 (SDA), U9.14 (SDA)
TOF_XSHUT_1: J4.1, R23.2, U5.2 (GPB5)
TOF_XSHUT_2: J4.2, R28.2, U5.3 (GPB6)
TOF_XSHUT_3: J4.3, R29.2, U5.4 (GPB7)
USB_N: J1.A7 (D-), J1.B7 (D-), U1.13 (IO19)
USB_P: J1.A6 (D+), J1.B6 (D+), U1.14 (IO20)
VBATT: C25.1, C26.1, C31.1, FB1.2, R18.2, R22.1, R25.1, TP3.1, TP4.1, U6.2 (VIN), U8.2 (S)
VBATT_SENSE: R25.2, R27.2, U1.4 (IO4)
VC: J3.2, R34.2
VMOT: C21.1, C23.1, C40.1, C41.2, C49.2, R19.2, TP7.1, U4.12 (VM), U8.3 (D), U10.10 (VIN), U10.11 (VIN), U10.12 (VIN), U10.13 (EN)
VMOT_EN: R26.1, U5.1 (GPB4)
VSERVO: C47.2, C48.1, C51.1, J7.1, L2.2, R32.2, R40.1, TP13.1, U10.14 (VOS)
VSS_SENSE: C44.1, C45.1, IC1.6 (VSS), J3.1, NT1.1
WIFI_LED: R9.1, U5.18 (GPA1)

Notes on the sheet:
VBATT Regulation
Net Setup
Battery Management System (BMS)
Vf = 2.8V, R = 100, If = 0.005A * 330 selected for dimness
Mounting Holes
To BMS
Fuse rated for 7A 12V TVS diode standoff @ 9V, breakdown @ 10V, clamps @ 15.4V
VBATT
S3 Decoupling
I2C Pullups
MCU Circuitry
Vout < 2.8V (S3 Docs) Vout = Vbatt * (R2) / (R1+R2) R1 = 100k R2 = (R1 * Vout) / (Vbatt - Vout) R2 = (100000 * 2.8) / (7.4 - 2.8) = 50k ≈ 47k
Power Indication & Voltage Sensing
BATT_N -> BMS ->
USB Connector
VBATT Protection & Conditioning
Manually set ROSC; by default, fsw = 120 kHz With 200k resistor, fsw ≈ 525 kHz (Inverse) Css (nF) = (tss (ms) * Iss (uA) / Vref (V) Iss = 2uA, Vref = 0.8V from datasheet Target start time of 5ms Css = 5 * 2.5 = 12.5 nf ≈ 10 nF (std value) Schottky Catch Diode Must be > Vin; V > 8.4V, Handle 2A outp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
π-Filter Ferrite Bead Isat = 1.5 * Inet Isat = 1.5 * 5 A ≈ 10 A Low heat dissipation. DCR = 10 mohm P = I^2 * DCR = (5A)^2 * (0.01) = 0.25 W (heat)
Dual H-Bridge Motor Driver
BATT_P -> PROT. -> FILTER ->
Motor Headers (N20)
SI2393DS chosen for RPP - Vds > (2x8.4V) ≈ 20V - Id < Inet ≈ 6A - P = I^2 * R = (5A)^2 * (0.0227) = 0.576 W (heat)
flyback diode to protect against inductive spikes
8-bit mode
5V MUX
VBATT | BUCK | PMUX (5V_USB) | LDO |
Twist and crimp SCL & SDA wires to form shared bus. Placed bulk and decoupling connectors.
MUXED 5V Regulation
IMU Interface
LED Diagnosis & Indication
VMOT
VL53L0X ToF Sensors Interface
Controlled VBATT for Motor Supply (VM)
BATT_PLUG
S3 Mode Select
I2C Bus
Inet = Imot + Iperiph Imot = nMotors * Imotors = 2 * 1.25 A = 2.50 A Iperiph ≈ 1 A Inet = 3.50 A Safety Margin: 1.25 * 3.50 A ≈ 5A = Inet
Vf = 2.1V, R = 68, If = 0.02A * 150 selected for dimness
VBATT | SW |
SYSTEM GND

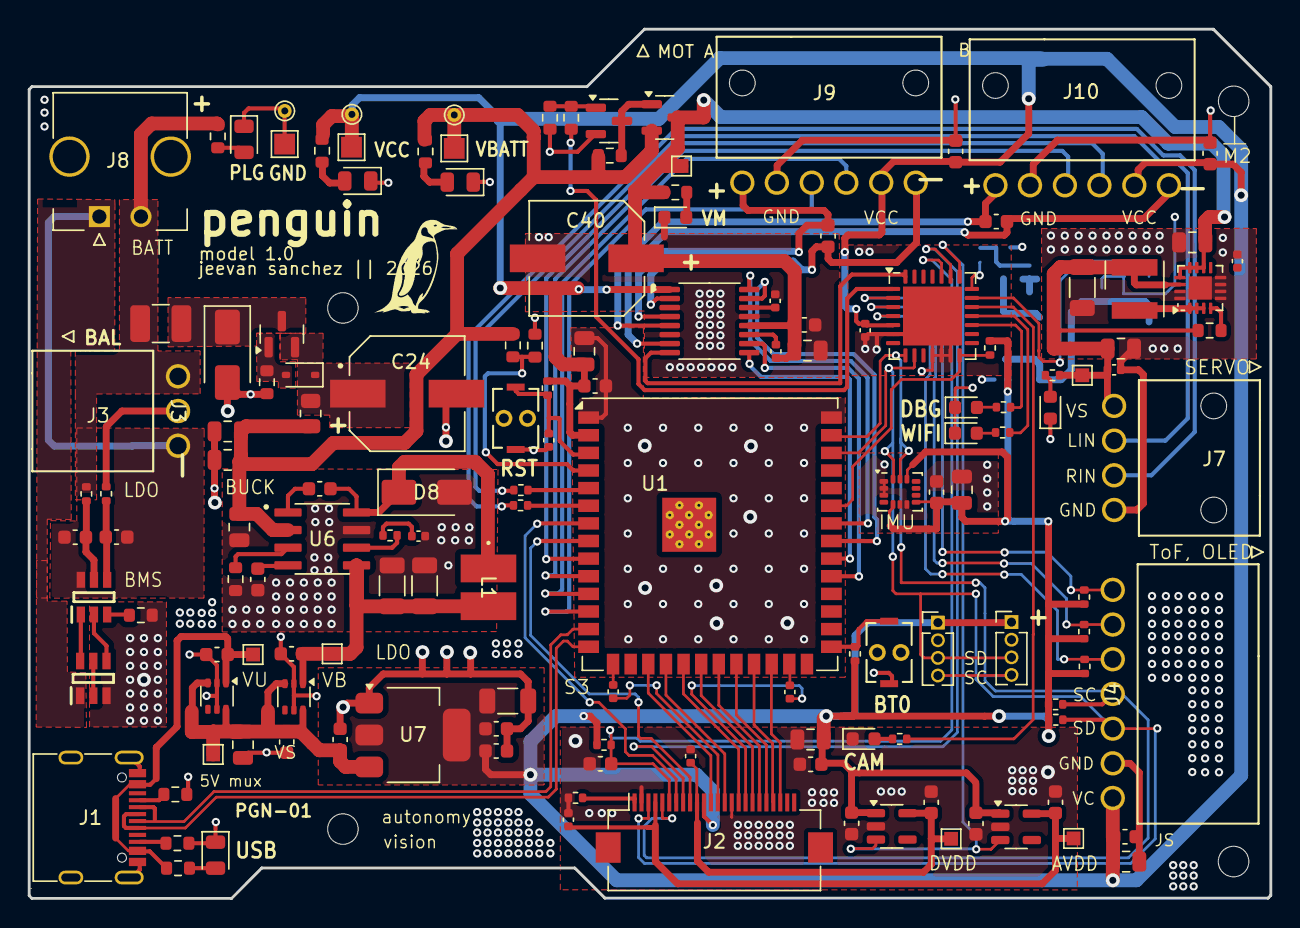
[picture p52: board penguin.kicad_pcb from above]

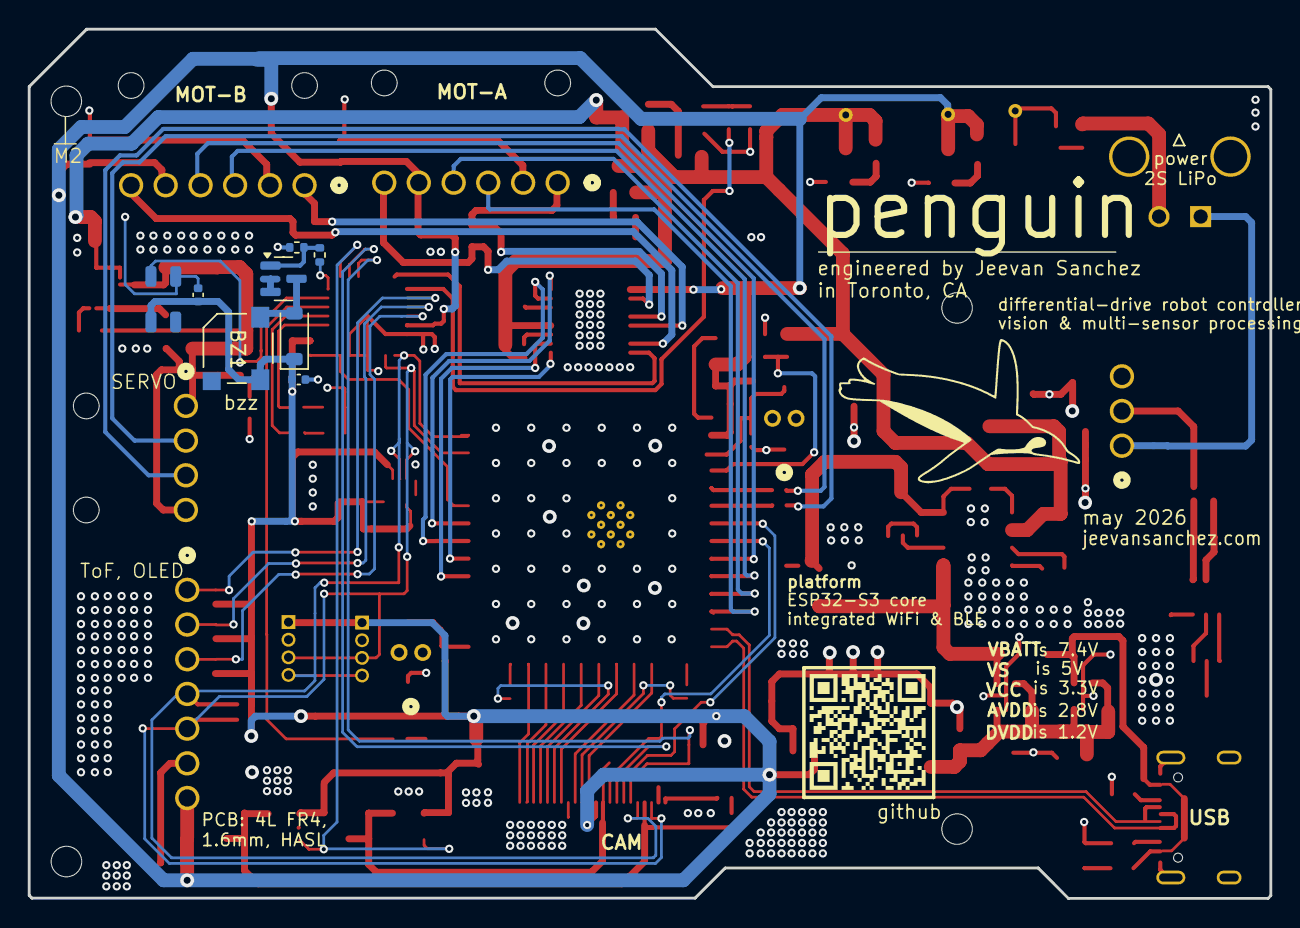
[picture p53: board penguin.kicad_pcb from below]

Board: 4 copper layers, 89.5 x 62.6 mm, 157 parts (9 on the bottom side), 101 nets.

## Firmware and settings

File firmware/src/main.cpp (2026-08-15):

/**
 * @file        main.cpp
 * @brief       Main entry point
 * @author      Jeevan Sanchez
 * @date        2026-06-29
 *
 * PENGUIN
 */

#include "config.hpp"
#include "test_bench.hpp"
#include "dashboard.hpp"
#include "scheduler.hpp"
#include "penguin_state.hpp"
#include "behaviour.hpp"
#include "locomotion.hpp"
#include "servo_driver.hpp"
#include "balance_controller.hpp"
#include "velocity_controller.hpp"
#include "motion_config.hpp"
#include "tof_driver.hpp"
#include "oled_driver.hpp"

bool menuShown = false;
CAMDriver cameraDriver;
HTTPServer http{cameraDriver};
bool dashboardRunning = false;
LSM6DSM imu;

BalanceController balanceController(MotionConfig::BAL_KP, MotionConfig::BAL_KI, MotionConfig::BAL_KD, MotionConfig::TURBO_SPEED);
VelocityController leftVController(MotionConfig::VEL_KP, MotionConfig::VEL_KI, MotionConfig::VEL_KD, 255);
VelocityController rightVController(MotionConfig::VEL_KP, MotionConfig::VEL_KI, MotionConfig::VEL_KD, 255);
ServoDriver hipL(Pins::MCU::L_SERVO);
ServoDriver hipR(Pins::MCU::R_SERVO);
IMUDriver imuDriver;
BattDataDriver battDriver;
constexpr uint16_t TOF_CORRECTION_MM = 60;
TOFDriver sensor1(Pins::MCP::TOF_XSHUT_1, 0x31, 100.0, TOF_CORRECTION_MM);
TOFDriver sensor2(Pins::MCP::TOF_XSHUT_2, 0x32, 100.0, TOF_CORRECTION_MM);
TOFDriver sensor3(Pins::MCP::TOF_XSHUT_3, 0x33, 100.0, TOF_CORRECTION_MM);
MotorDriver motorL(Pins::MCU::MOTA_IN1, Pins::MCU::MOTA_IN2, Pins::MCU::ENC_A_PH1, Pins::MCU::ENC_A_PH2);
MotorDriver motorR(Pins::MCU::MOTB_IN1, Pins::MCU::MOTB_IN2, Pins::MCU::ENC_B_PH1, Pins::MCU::ENC_B_PH2);

Locomotion locomotion(balanceController, leftVController, rightVController, motorL, motorR, hipL, hipR);
Behaviour behaviour;

Scheduler scheduler(imuDriver, battDriver, sensor1, sensor2, sensor3, motorL, motorR);

namespace
{
bool initializeTofSensor(const char *label, TOFDriver &sensor)
{
    sensor.off();

    if (sensor.begin())
    {
        Serial.printf("%s --initialized\n", label);
        return true;
    }

    Serial.printf("%s init failure\n", label);
    return false;
}

void initializeAllTofSensors()
{
\    sensor1.off();
    sensor2.off();
    sensor3.off();
    delay(30);

    initializeTofSensor("TOF L", sensor1);
    initializeTofSensor("TOF M", sensor2);
    initializeTofSensor("TOF R", sensor3);
}

bool initializeIMU()
{
    if (!imuDriver.begin())
    {
        Serial.println("IMU init failure");
        return false;
    }

    Serial.println("IMU --calibrating | hold still");
    delay(100);
    imu.calibrateGyro(200);
    Serial.println("IMU --calibrated");
    return true;
}

void recoverSensors(bool force = false)
{
    static uint32_t lastHealthCheck = 0;
    uint32_t now = millis();

    if (!force && (now - lastHealthCheck < 1000))
    {
        return;
    }

    lastHealthCheck = now;

    if (force)
    {
        Serial.println("TOF --manual full recovery");
        recoverI2C();

        if (!probeI2C(0x20))
        {
            Serial.println("MCP --reinitializing");
            if (!init_mcp())
            {
                Serial.println("MCP reinit failure");
                return;
            }
        }

        initializeAllTofSensors();
        return;
    }

    if (force || !sensor1.ping())
    {
        Serial.println(force ? "TOF L --manual recover" : "TOF L --offline, reinitializing");
        initializeTofSensor("TOF L", sensor1);
    }

    if (force || !sensor2.ping())
    {
        Serial.println(force ? "TOF M --manual recover" : "TOF M --offline, reinitializing");
        initializeTofSensor("TOF M", sensor2);
    }

    if (force || !sensor3.ping())
    {
        Serial.println(force ? "TOF R --manual recover" : "TOF R --offline, reinitializing");
        initializeTofSensor("TOF R", sensor3);
    }
}
}

void displayMenu()
{
    Serial.println("\n--- PENGUIN ---");
    Serial.println(" [space] : launch dashboard");
    Serial.println(" [t] : launch test bench");
    Serial.println(" [s] : scan I2C bus");
    Serial.println(" [r] : recover sensors"); 
    Serial.println("------------------------");
}

void runDash()
{
    Serial.println("\n>> ---launching dashboard");
    run_dashboard();
}

void runTaskT()
{
    Serial.println("\n>> ---launching test bench");
    run_test_bench();
}

void runTaskS()
{
    if (!probeI2C(0x20))
    {
        recoverI2C();
    }
    delay(50);

    Serial.println("\n>> ---scanning I2C bus");
    scanI2C();
    delay(1000);
}

void runTaskR() {
    Serial.println("\n>> --recovering sensors");
    recoverSensors(true);
}
void setup()
{
    Serial.begin(921600);

    pinMode(Pins::MCU::MCP_RESET, OUTPUT);
    digitalWrite(Pins::MCU::MCP_RESET, HIGH);

    delay(50);

    while (!Serial && millis() < 4000)
    {
        delay(10);
    }

    Serial.println("\n==============================");
    Serial.println("PENGUIN ---initializing");

    if (init_mcp())
    {
        Serial.println("PENGUIN ---initialized");
    }
    else
    {
        Serial.println("MCP init failure");
    }
    oledLoadingScreen(0);

    initializeAllTofSensors();

    if (cameraDriver.begin())
    {
        Serial.println("CAM --initialized");
    }
    else
    {
        Serial.println("CAM init failure");
    }
    oledLoadingScreen(25);

    mcp.pinMode(Pins::MCP::CAM_LED, OUTPUT);
    mcp.pinMode(Pins::MCP::DBG_LED, OUTPUT);
    mcp.pinMode(Pins::MCP::WIFI_LED, OUTPUT);
    oledLoadingScreen(50);

    initializeIMU();
    oledLoadingScreen(75);

    led_startup();
    oledLoadingScreen(85);
    displayMenu();

    motorL.begin();
    motorR.begin();
    oledLoadingScreen(90);
    hipL.begin(MotionConfig::DEFAULT_HIP_ANGLE, MotionConfig::MAX_HIP_ANGLE);
    hipR.begin(MotionConfig::DEFAULT_HIP_ANGLE, MotionConfig::MAX_HIP_ANGLE);
    oledLoadingScreen(95);

    behaviour.begin();
    oledLoadingScreen(100);
    delay(400);
}

void loop()
{
    if (blinksRemaining > 0)
    {
        blinkP(activeBlinkPin, blinkCount);
    }

    runDash();

    scheduler.update(penguin_state);
    recoverSensors();

    static uint32_t last = millis();
    uint32_t now = millis();

    float dt = (now - last) / 1000.0f;
    last = now;

    behaviour.update(penguin_commands, penguin_state, dt);
    locomotion.update(penguin_state, penguin_commands, dt);

    oled();

    if (dashboardRunning)
    {
        http.update(penguin_state);
    }

    if (!menuShown && millis() > 5000)
    {
        displayMenu();
        menuShown = true;
    }

    if (Serial.available() > 0)
    {
        char choice = Serial.read();
        menuShown = true;

        switch (choice)
        {
        case 't':
        case 'T':
            runTaskT();
            displayMenu();
            break;

        case 's':
        case 'S':
            runTaskS();
            displayMenu();
            break;

        case ' ':
            runDash();
            break;

        case 'r':
        case 'R':
            runTaskR(); 
            break;

        case 'm':
        case 'M':
            displayMenu();
            break;

        case '\n':
        case '\r':
            break;

        default:

            break;
        }
    }
    delay(1);
}

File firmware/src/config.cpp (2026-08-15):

/**
 * @file        config.cpp
 * @brief       System configuration and utility.
 * @author      Jeevan Sanchez
 * @date        2026-06-29
 *
 * PENGUIN
 */

#include "config.hpp"

const char* ssid = "Health2024";
const char* pswd = "Rexdale2024";

Adafruit_MCP23X17 mcp;

int blinksRemaining = 0;
unsigned long lastBlink = 0;
uint8_t activeBlinkPin = 0;
int blinkCount = 0;

bool init_mcp(void) {
    Wire.begin(Pins::MCU::SDA, Pins::MCU::SCL, 100000);
    
    if (!mcp.begin_I2C()) {
        return false; 
    }
    return true;
}

void led_startup(void) {
    mcp.digitalWrite(Pins::MCP::CAM_LED, HIGH);
    delay(400);
    mcp.digitalWrite(Pins::MCP::CAM_LED, LOW);
    delay(400); 

    mcp.digitalWrite(Pins::MCP::DBG_LED, HIGH);
    delay(300);
    mcp.digitalWrite(Pins::MCP::DBG_LED, LOW);
    delay(300); 

    mcp.digitalWrite(Pins::MCP::CAM_LED, HIGH);
    delay(200);
    mcp.digitalWrite(Pins::MCP::CAM_LED, LOW);
    delay(200);
    mcp.digitalWrite(Pins::MCP::DBG_LED, HIGH);
    delay(200); 

    mcp.digitalWrite(Pins::MCP::DBG_LED, LOW);
    mcp.digitalWrite(Pins::MCP::CAM_LED, HIGH);
    delay(200);
    mcp.digitalWrite(Pins::MCP::CAM_LED, LOW);
    delay(200); 
}

void blinkLED(uint8_t ledPin, int count, int delayMs) {
    for(int i = 0; i < count; i++) {
        mcp.digitalWrite(ledPin, HIGH);
        delay(delayMs);
        mcp.digitalWrite(ledPin, LOW);
        delay(delayMs);
    }
}

void scanI2C() {
    Serial.println("scanning I2C bus...");
    for(byte address = 1; address < 127; address++) {
        Wire.beginTransmission(address);
        if (Wire.endTransmission() == 0) {
            Serial.printf("Found device at 0x%02X\n", address);
        }
    }
}

bool probeI2C(uint8_t address) {
    Wire.beginTransmission(address);
    return Wire.endTransmission() == 0;
}

void recoverI2C() {
    Wire.end(); 
    delay(10);

    pinMode(Pins::MCU::SDA, INPUT_PULLUP);
    pinMode(Pins::MCU::SCL, INPUT_PULLUP);
    delay(10);

    const bool busStuck = (digitalRead(Pins::MCU::SDA) == LOW);

    if (busStuck) {
        pinMode(Pins::MCU::SCL, OUTPUT);

        for (int i = 0; i < 16; i++) {
            digitalWrite(Pins::MCU::SCL, LOW);
            delayMicroseconds(10);
            digitalWrite(Pins::MCU::SCL, HIGH);
            delayMicroseconds(10);
        }

        pinMode(Pins::MCU::SDA, OUTPUT);
        digitalWrite(Pins::MCU::SDA, LOW);
        delayMicroseconds(10);
        digitalWrite(Pins::MCU::SCL, HIGH);
        delayMicroseconds(10);
        digitalWrite(Pins::MCU::SDA, HIGH);
        delayMicroseconds(10);
    }

    Wire.begin(Pins::MCU::SDA, Pins::MCU::SCL); 
}


// non-blocking led stuff

void blinkP(uint8_t pin, int count) {
    if (blinksRemaining == 0) blinksRemaining = count * 2;

    if (millis() - lastBlink > 200) {
        lastBlink = millis();
        bool current = mcp.digitalRead(pin);
        mcp.digitalWrite(pin, !current);
        blinksRemaining--;

        if (blinksRemaining == 0) mcp.digitalWrite(pin, LOW);
    }
}

float lerp(float current, float target, float rate, float dt) {
    // move current to target smoothly based on rate
    return current + (target - current) * (1.0f - expf(-rate * dt));
}

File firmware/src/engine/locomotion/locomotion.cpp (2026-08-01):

/**
 * @file        locomotion.cpp
 * @brief       Implementation of core locomotion engine and controller orchestrator
 * @author      Jeevan Sanchez
 * @date        2026-07-27
 *
 * PENGUIN
 */


#include <Arduino.h>
#include "locomotion.hpp"

/// @brief construct with all locomotive hardware (via drivers) and controllers 
Locomotion::Locomotion(BalanceController &balance, VelocityController &leftVController, VelocityController &rightVController, MotorDriver &motorL, MotorDriver &motorR, ServoDriver &hipL, ServoDriver &hipR) 
: _balance(balance), _leftVController(leftVController), _rightVController(rightVController), _motorL(motorL), _motorR(motorR), _hipL(hipL), _hipR(hipR) {}

void Locomotion::update(const PenguinState &state, const PenguinCommands &commands, float dt) {
    float balanceOutput = _balance.update(state.imu, commands.targetPitch, dt); // RPM output produced by balance PID

    WheelTargets targets = calculateWheelTargets(commands, balanceOutput); // convert to differential-drive inputs

    // update left/right velocity controllers with PID-produced differential-drive inputs
    float leftPWM = _leftVController.update(state.motorL, targets.leftRPM, dt); 
    float rightPWM = _rightVController.update(state.motorR, targets.rightRPM, dt); 

    _motorL.run(leftPWM); 
    _motorR.run(leftPWM);     

    // observe commands for hip-servo writes
    _hipL.write(commands.leftHipAngle); 
    _hipR.write(commands.rightHipAngle); 
}

// L/R_SPEED = FWD_INPUT - TURN_INPUT + CORRECTION_INPUT
WheelTargets Locomotion::calculateWheelTargets(const PenguinCommands &commands, float balanceOutput) {
    WheelTargets targets; 

    targets.leftRPM = commands.forwardRPM - commands.turnRPM + balanceOutput; 
    targets.rightRPM = commands.forwardRPM - commands.turnRPM + balanceOutput; 

    return targets; 
} 

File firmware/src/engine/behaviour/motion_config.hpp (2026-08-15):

/**
 * @file        motion_config.hpp
 * @brief       Motion constants & controller tuning 
 * @author      Jeevan Sanchez
 * @date        2026-07-30
 *
 * PENGUIN
 */

#pragma once 

#include <Arduino.h>

/// @brief constants for system configuration
// stance-based hip-servo angles 
// motor speeds based on levels and actions
// offsets for scan-pivots
// pitch depth (angles) for stance 
namespace MotionConfig {
    // tune
    constexpr float DEFAULT_HIP_ANGLE = 40.0f; 
    constexpr float SQUAT_HIP_ANGLE = 20.0f; 
    constexpr float STAND_HIP_ANGLE = 70.0f; 
    constexpr float LEFT_HIP_LEFT_LEAN_ANGLE = 0.0f; 
    constexpr float RIGHT_HIP_LEFT_LEAN_ANGLE = 0.0f; 
    constexpr float LEFT_HIP_RIGHT_LEAN_ANGLE = 0.0f; 
    constexpr float RIGHT_HIP_RIGHT_LEAN_ANGLE = 0.0f; 

    constexpr float CRAWL_SPEED = 50.0F;
    constexpr float CRUISE_SPEED = 150.0f; 
    constexpr float TURBO_SPEED = 250.0f; 

    constexpr float SPIN_STARTUP_SPEED = 50.0f;  

    constexpr float PIVOT_OFFST = 30.0f;
    constexpr float FWD_LEAN_PITCH = 5.0f; 

    // PID constants
    constexpr float BAL_KP = 40.0f; 
    constexpr float BAL_KI = 0.0f; 
    constexpr float BAL_KD = 0.5f; 

    constexpr float VEL_KP = 0.25f; 
    constexpr float VEL_KI = 0.0f; 
    constexpr float VEL_KD = 0.005f; 

    constexpr float MAX_HIP_ANGLE = 90;
}; 

/// @brief timing config for routines
namespace RoutineConfig {
    constexpr float SPEED_LERP_RATE = 5.0f;
    constexpr float PIVOT_LERP_RATE = 6.0f;

    constexpr float DEFAULT_STEP_DURATION = 3.0f;

    constexpr float STARTUP_SQUAT_DURATION = 0.5f;
    constexpr float STARTUP_PAUSE_DURATION = 0.5f;
    constexpr float STARTUP_SPIN_DURATION = 3.0f;

    constexpr float DRIVE_CRUISE_DURATION = 5.0f;
    constexpr float DRIVE_SQUAT_DURATION  = 2.5f;
    constexpr float DRIVE_TURBO_DURATION  = 2.0f;
    constexpr float DRIVE_CRAWL_DURATION  = 5.0f;

    constexpr float PATROL_CRUISE_DURATION = 4.0f;
    constexpr float PATROL_SCAN_DURATION   = 2.0f; 

    constexpr float EVASIVE_REVERSE_DURATION = 2.0f;
    constexpr float EVASIVE_RECOVER_DURATION = 2.0f;
}

/// @brief cascade speed structure 
enum class SpeedLevel {
    CRAWL,
    CRUISE, 
    TURBO
};

/// @brief getter for speed values (RPM) based on typed speed levels
/// used to update commands
/// @param level one of the three speed levels
/// @return the corresponding float RPM value
inline float getRPM(SpeedLevel level) {
    switch(level) {
        case SpeedLevel::CRAWL: return MotionConfig::CRAWL_SPEED; 
        case SpeedLevel::CRUISE: return MotionConfig::CRUISE_SPEED; 
        case SpeedLevel::TURBO: return MotionConfig::TURBO_SPEED;
        default: return 0.0f; 
    }
}

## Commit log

2026-05-13 add schematics
    [1053131102.step, 1053131107.stp, 1053131203.stp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]
2026-05-14 finalize board outline
    [penguin.kicad_pcb, penguin.kicad_sch]
2026-05-16 finsih front silkscreen
    [penguin.kicad_pcb, penguin.kicad_sch]
2026-05-16 finish back silkscreen
    [penguin.kicad_pcb]
2026-05-17 add IMU and redo BMS pours
    [penguin.kicad_pcb, penguin.kicad_sch]
2026-05-17 add servo connector
    [1053131102.step, 1053131107.stp, 1053131203.stp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]
2026-05-18 added servo
    [penguin.kicad_pcb, penguin.kicad_sch]
2026-05-18 finish hardware review
    [penguin.kicad_pcb, penguin.kicad_sch]
2026-06-22 add models
    [RC wheel.step, U_Channel_Lock.step, [3879] Servo Motor Horn for MG995 MG996 Series Motor SunRobotics_in_fron.step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]
2026-06-25 new board imgs
2026-06-26 remove DNP flags for pics
    [penguin.kicad_sch]
2026-06-27 power docs
2026-06-27 motor docs
    [penguin.kicad_sch]
2026-06-30 power test code
